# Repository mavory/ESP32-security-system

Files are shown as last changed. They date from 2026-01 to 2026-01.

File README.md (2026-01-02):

# ESP32 security system

It is a secure system that can use an RFID reader to let people into a building,...

## Why did I do this?

I don't even know... I previously did this project with an Arduino and so I decided to do it with my new ESP32!

## Features

- Web interface
- Can add new cards to the system (UID)
- It has a buzzer and an RGB LED for notification
- The motor acts like an automatic door

## Scripts

The entire script is only one and has about 300 lines, so just upload it via Arduino IDE and everything should work.

## How it works?

The RFID reader waits for the UID, if it is enabled in the system, the **motor** will turn, if not, it will not let you in. Turning the **buzzer** on or off can be controlled via a website running on the **IP address**.
- _Host mode:_ It can temporarily grant permission to a card for 2 minutes, and it can be extended or canceled
- _Lockdown mode:_ You can turn this mode on manually or set a time when it will turn on and turn off later. When it is on, the card cannot be scanned at that time and I cannot add a new card.
- _Scan new tag:_ You can add a tag permanently and change its name or remove it
- _Release latch:_ You can open the door manually
- You can also turn on/off the LED, buzzer, reader,...

### Home page:

### Admin page:


## 3D models

Here is a view of the top and bottom of the case:

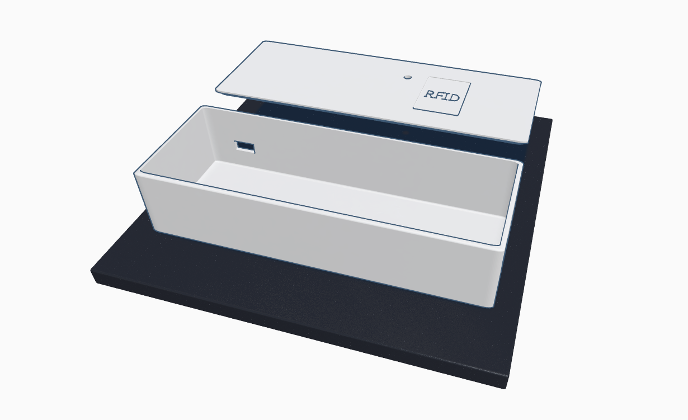
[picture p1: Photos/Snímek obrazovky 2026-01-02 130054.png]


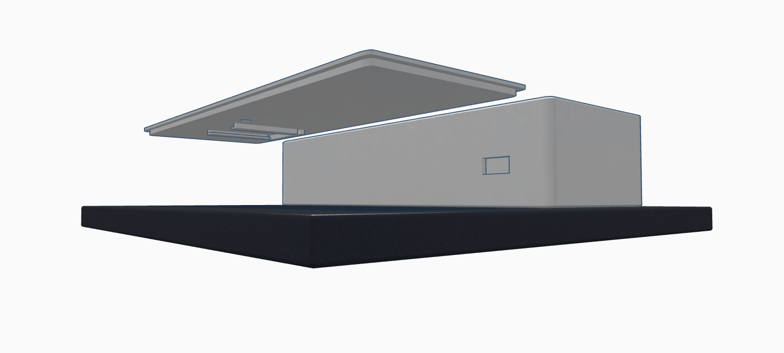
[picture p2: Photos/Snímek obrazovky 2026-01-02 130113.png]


## There is the final video of how it works!

_Here is a youtube video where you can see how it works:_ [Link](https://youtu.be/qIwMznMcJI0)



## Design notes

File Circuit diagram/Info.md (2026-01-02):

Documentation for the ESP32 RFID locking system!!

## Wiring

### RFID Reader (MFRC522)
- SDA (SS): GPIO 21
- SCK: GPIO 18
- MOSI: GPIO 23
- MISO: GPIO 19
- RST: GPIO 22
- 3.3V: 3.3V
- GND: GND

### Stepper Motor (ULN2003 Driver)
- IN1: GPIO 32
- IN2: GPIO 33
- IN3: GPIO 27
- IN4: GPIO 14
- VCC: 5V (External)
- GND: GND

### RGB LED Indicator
- Red: GPIO 25
- Green: GPIO 26
- Blue: GPIO 4
- GND: GND

### Buzzer
- Pin: GPIO 2
- GND: GND

---

## Technical Notes
- **Power:** The RFID module must be powered by 3.3V. Using 5V will damage the chip!

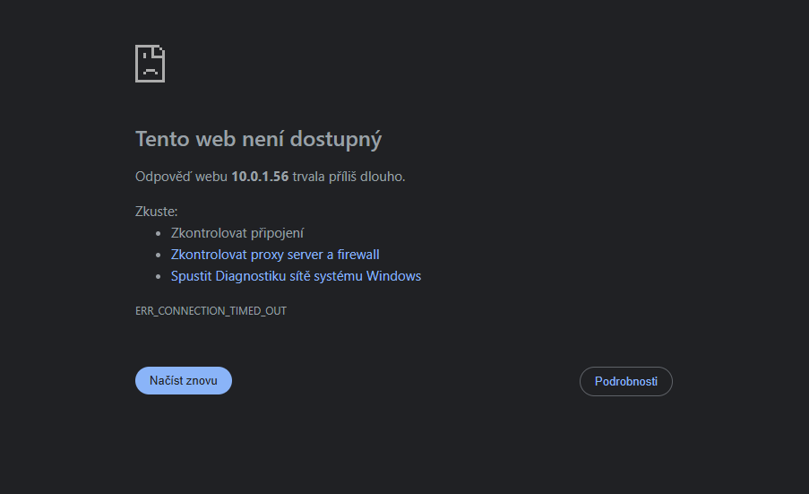
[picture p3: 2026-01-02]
Photos/Snímek obrazovky 2026-01-01 231753.png

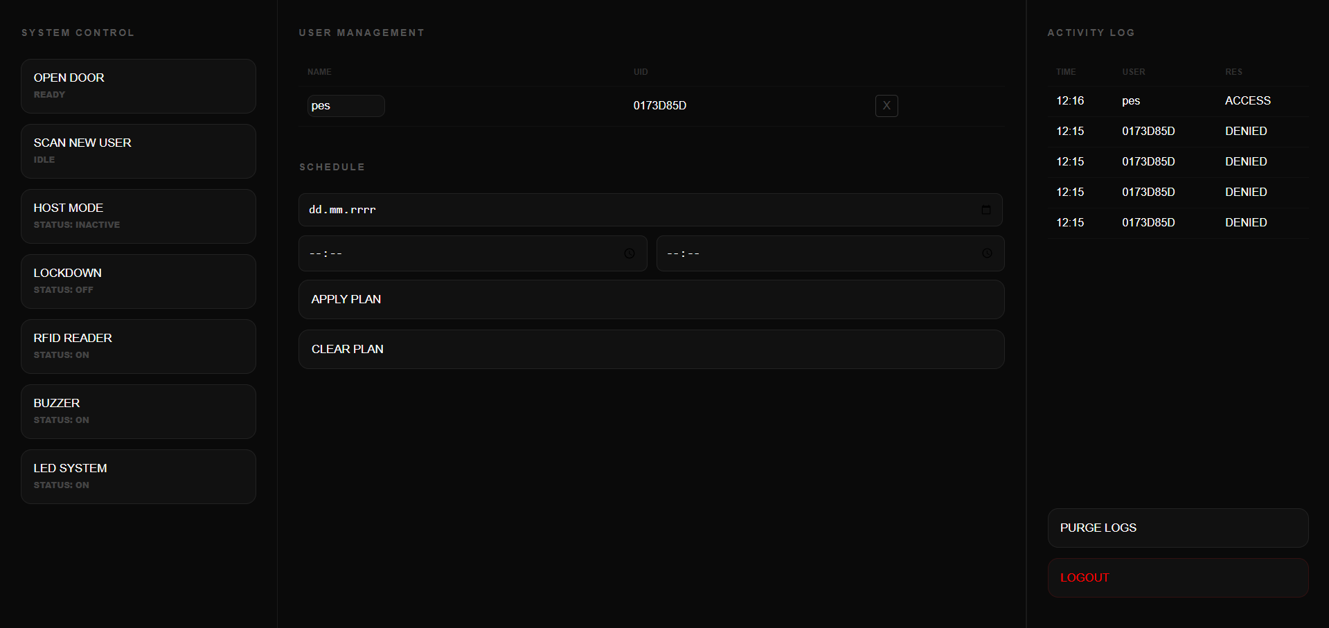
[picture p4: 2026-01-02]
Photos/Snímek obrazovky 2026-01-02 121619.png

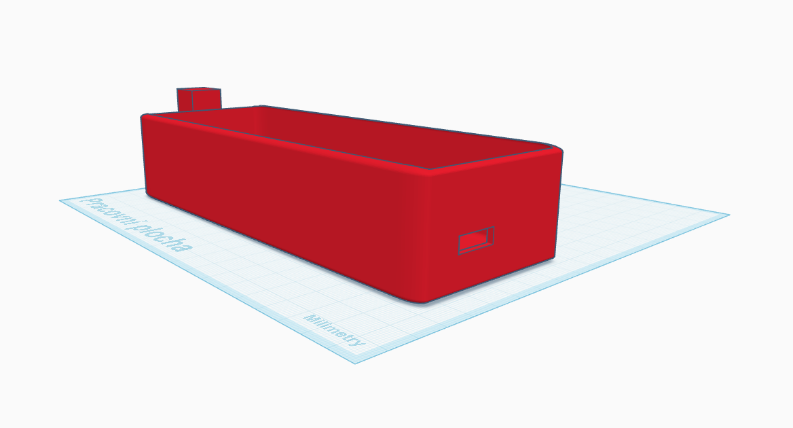
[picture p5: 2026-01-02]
Photos/Snímek obrazovky 2026-01-02 115620.png

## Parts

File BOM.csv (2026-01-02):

Item | Quantity | Link
ESP32 | 1 | https://www.aliexpress.com/item/1005009694232832.html?curPageLogUid=bPYYmnweQOZ8
RGB led | 1 | https://www.aliexpress.com/item/32977462875.html?scm_id=1007.40050.354490.0&scm-url=1007.40050.354490.0
Stepper motor | 1 | https://www.aliexpress.com/item/1005009055737108.html?curPageLogUid=D6r5ZVVTdLbr
Breadboard | 1 | https://www.aliexpress.com/item/1005009799908389.html
RFID module | 1 | https://www.aliexpress.com/item/1005001565846229.html
Buzzer | 1 | https://www.aliexpress.com/item/1005006260328559.html?curPageLogUid=u9zf8d5xh8uM
Cables | Idk...Much | https://www.aliexpress.com/item/1005002611994443.html?curPageLogUid=fx2zB0EGcu5H

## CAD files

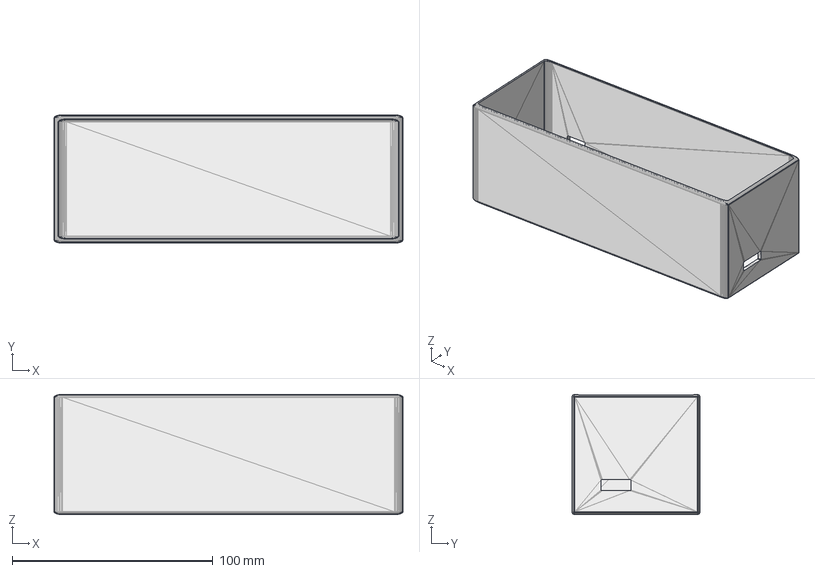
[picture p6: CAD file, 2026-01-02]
CAD/V2_Case.step
174.0 x 64.0 x 60.0 mm

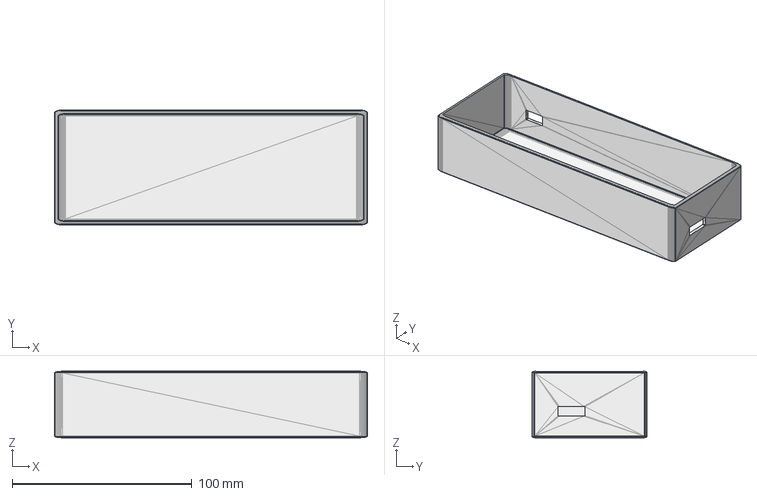
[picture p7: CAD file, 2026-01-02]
CAD/Case.step
174.0 x 64.0 x 37.0 mm

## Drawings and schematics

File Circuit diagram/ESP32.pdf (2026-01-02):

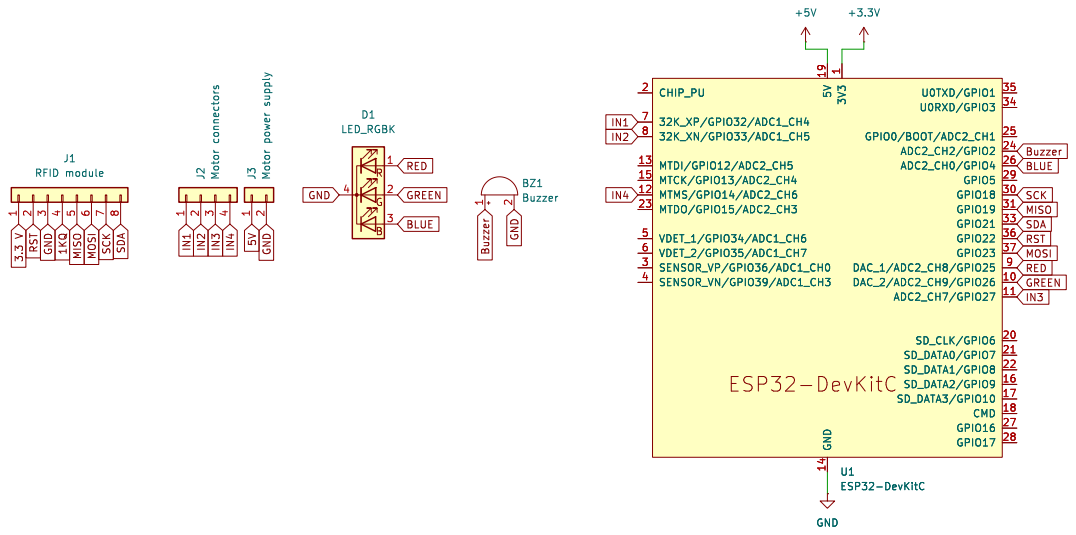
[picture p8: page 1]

Buzzer
BLUE
RST SCK GREEN MISO

2 BZ1 Buzzer SCK SDA IN1 IN45V IN3 GND IN2 MOSI

File: ESP32.kicad_sch Sheet: /
Id: 1/1 Title: ESP32 security system

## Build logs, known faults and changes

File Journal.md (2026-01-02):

# My Journal

This is a diary where I describe everything about how I created this project.

## So how much time did I spend on that?

I think I spent about 26.5 hours on this project.

## My worst hangups

- Unfortunately, I designed the bottom part of the case incorrectly, so I had to redo it completely.
- My RFID module hasn't been working for a while, so I had to solve this error as well.
- The website also didn't work for me because I broke it completely while coding.

## Timeline

### The beginning of my project!
I wanted to create an Arduino RFID system first, but later I decided to remake it and make it on my new ESP32!
I had to start from scratch, so I thought about how everything would work. I thought I could put a motor as a door and everything would be controlled via the web. When I had everything ready, I started taking things apart.
So it took me about 1.5 hours, because I had to dismantle the old project and think about the new one.



### Oh no! Breadboard problem
When my brain was ready, I started taking things apart and adjusting things on the breadboard!
I thought it would be fun, but it wasn't at all...
The ESP32 didn't fit on my breadboard and unfortunately I don't have another one, so I spent some time thinking about how to solve this problem.
Unfortunately, I struggled with this problem for quite a long time, because I was looking for other solutions, such as trying to solder it, but I backed away from that.
I came up with a solution, which is to put the ESP32 aside and thus have to use 2x more jumpers.



### Connecting things is my passion..
So when I solved this problem, I started wiring all the components, I have to say it was terrible.
I had to redo the whole layout a few times just to make sure everything fit on the breadboard.
I managed it and then I moved on to the next part!



### First steps to working code
Then I started coding. At first I tested if everything worked and I had to read some articles about how ESP32 works, because that was my first project with this microcontroller.
It took me about half an hour, but then I found out that it is very similar to Arduino!
So then everything went like clockwork (that's what I thought...) - Unfortunately, I had a lot of problems with the micro SD card reader, then with RFID,... but I managed it



### Big mistake for me
I thought everything would be fine, but after redoing the wiring, everything fell apart, the SD card reader and RFID reader didn't work, the RGB diode didn't light up properly, so I had to disconnect everything again and slowly start over.
I connected some pins and suddenly everything started working - for now...
( I didn't know I would have to do it again 💀 )



### A new beginning - for now
Well... I started coding again. Everything went pretty well, except for one thing. The SD card reader suddenly stopped working, so I tried to make a code for it to see if it would work now, and unfortunately, it didn't.
But I researched this bug for a long time because I couldn't figure it out.
This way, I was forced to remove the micro SD reader and live without it. I rewrote the entire code to make it work without the reader.



### Coding a script for ESP32
After this bug, I finally started coding and I have to say that it was terrible, my server crashed several times, it wouldn't load (as you can see in the photo) and I didn't know what to do.
Well, I tried different methods, but after a while I still ended up with the IP address.



### 1. Web interface
Coding was probably the hardest part for me, even though I made a lot of mistakes elsewhere. Coming up with a nice, but functional web interface was beyond my skills.
I tried to make just an admin panel without security, but that seemed strange to me, so I also tried to make a page for the public where they can see statistics and then I tried to make an admin page, which I didn't succeed at all. Either it wouldn't load at all or I couldn't connect the website to the ESP32.



### My dream look
I wasn't at all satisfied with how the temporary web interface looked, so I started reworking the code to get my dream look.
It took me a lot of effort, I tried a lot of options, but again I encountered an error that I had been solving for a long time, but after about half an hour it was solved and I could continue!
After some time, I decided that a modern and minimalist look with just a black and white theme would be best.



### Case design for everything
I took a break from programming for now and started thinking about how I would put everything in the case to make it look good!
My favorite and easy program to learn is Tinkercad. I normally use Fusion, but this is faster for me. When I started making some designs, I didn't notice that I was supposed to add a little space, so I fixed that. I had the sketch ready and suddenly I remembered that I was out of filament, so I ordered some new ones and hopefully they will arrive in the morning!



### A moment for quick coding
I had nothing else to do, so I started redesigning the web interface. It took me a while, but I still wasn't satisfied... At least it was a black and white look and minimalist.
Some buttons just didn't work properly, so I had to redesign it again later, but at least I knew where it was going.



### How to hide an RFID module?
I got my filament today, so I can start modeling the case! But first I have to measure everything so that everything fits in the case.
I had to measure mainly the RFID module so that they could make a smaller space for it to fit in there.
I thought for a while about how I would do it and came up with a solution: I would make a holder for the top part to hold it so it wouldn't be visible, but it should work.



### Making all parts of the case
It took me a while, but I've finished both parts of the case. There's a hole on the top for the RGB diode that signals the status, and there's also a marked hole for the RFID!

- Here is the top view:



- Here is the bottom view:



### 2. Web interface
Once I had the models ready, I went back to coding the website. There were some errors there, so I had to fix them. Sometimes the button wouldn't work for me or sometimes "Host mode" wouldn't work for me, so I fixed all that.
Unfortunately, I still have to redo the code, probably one more time, because I want to add some very interesting things!



### Circuit diagram!
I remembered that I still need to finish the Circuit diagram to show how it's connected. So I opened my favorite program - KICAD!
I started creating, but for example, for ESP32 I didn't know which model to use, I did some research and had to download some libraries to make it as similar as possible, but I managed it quite quickly, in my experience, in about an hour and a half.
The hardest part for me was probably finding what symbols to use, for example, I didn't know what symbol to use for the motor, but I guess I got the hang of it.

- Circuit diagram:



### Printing 3D models
I'm already printing the first part! Hopefully it will work and everything will fit.
Unfortunately, I've found a problem that when I want to scan the UID, the reader doesn't work at all, so I have to try to find the problem and solve it as quickly as possible!



### Final code for the website
I have to say it with joy, but I already have a finished web interface, which looks very good to me! There are buttons to turn off the buzzer, RGB diodes, readers,...
It all took me a lot of time and I have to say that it was worth it. The code is about 330 lines, so it's not that long. I also modified the homepage to match the new design.

- Home page:



- Admin page:



### Exporting files
I'm very close to the end, just need to finish a few wiring things and I think it'll be ready! I already have the last part printed, but the supports were harder to remove, so I had to spend 30 minutes cutting the plastic to make it fit properly!
I've also started exporting the files, which I'll later upload to GitHub, where everything is! I still have to finish the information and connections, so I still have a long way to go.



### Remaking a 3D model
How to say it.... I started putting all the things in the box, everything fit except for one SMALL THING... CABLES
I made the box too short, so I can't close the cables and so on with it anymore. So I had to redo the case again and hopefully it will be good.



### GitHub editing
So I started 3D printing the case, but I decided to print it in white and the top in black! In the meantime, I continued to write and upload things to GitHub to make sure everything met the requirements.
I'm very excited that I got through all the hurdles, because at first I thought I just couldn't do it.
For now, I've made a BOM, I've also uploaded the completed code, I've uploaded the Circuit diagram and some information to make it easier to connect.



### Putting things in the case
I finished the last part - the case. It took me a while to remove the supports, cut off the gaps and I really like this design! The cable to the motor runs from the side and the power cable that powers the ESP32 runs from the back!
I glued the top with normal super glue and put the buzzer close to the hole so that it would be better heard, but I decided that I would still edit the code in the end to fine-tune the RFID, but mainly to increase the "volume" of the buzzer, because it was not audible before.



**After about +- 26.5 hours I have finished this project and I am very proud of it. I was able to create my first project with ESP32!**
## How it works:
The RFID reader waits for the UID, if it is enabled in the system, the **motor** will turn, if not, it will not let you in. Turning the **buzzer** on or off can be controlled via a website running on the **IP address**.
After **10 attempts**, the reader is blocked for a while to prevent unknown cards from being tried over and over again.
- _Host mode:_ It can temporarily grant permission to a card for 2 minutes, and it can be extended or canceled
- _Lockdown mode:_ You can turn this mode on manually or set a time when it will turn on and turn off later. When it is on, the card cannot be scanned at that time and I cannot add a new card.
- _Scan new tag:_ You can add a tag permanently and change its name or remove it
- _Release latch:_ You can open the door manually
- You can also turn on/off the LED, buzzer, reader,...

_Here is a youtube video where you can see how it works:_ [Link](https://youtu.be/qIwMznMcJI0)

## Wiring:

### RFID Reader (MFRC522)
- SDA (SS): GPIO 21
- SCK: GPIO 18
- MOSI: GPIO 23
- MISO: GPIO 19
- RST: GPIO 22
- 3.3V: 3.3V
- GND: GND

### Stepper Motor (ULN2003 Driver)
- IN1: GPIO 32
- IN2: GPIO 33
- IN3: GPIO 27
- IN4: GPIO 14
- VCC: 5V (External)
- GND: GND

### RGB LED Indicator
- Red: GPIO 25
- Green: GPIO 26
- Blue: GPIO 4
- GND: GND

### Buzzer
- Pin: GPIO 2
- GND: GND

### Technical Notes
- **Power:** The RFID module must be powered by 3.3V. Using 5V will damage the chip!

## Scripts
The entire script is only one and has about **300 lines**, so just upload it via **Arduino IDE** and everything should work.

## Libraries:

```
- MFRC522.h
- ESPAsyncWebServer.h
- AsyncTCP.h
- Stepper.h
```

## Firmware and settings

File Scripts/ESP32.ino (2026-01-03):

#include <Arduino.h>
#include <SPI.h>
#include <MFRC522.h>
#include <LittleFS.h>
#include <WiFi.h>
#include <ESPAsyncWebServer.h>
#include <Stepper.h>
#include <deque>
#include "time.h"

// PINOUT!!
const char* ssid = "WIFI";
const char* password = "PASS";
const char* adminUser = "admin";
const char* adminPass = "admin123";

#define SCK_PIN 18
#define MISO_PIN 19
#define MOSI_PIN 23
#define SS_PIN 21
#define RST_PIN 22
#define STEP1 32
#define STEP2 33
#define STEP3 27
#define STEP4 14
#define L_R 25
#define L_G 26
#define L_B 4
#define BUZZ 2

//udání
MFRC522 rfid(SS_PIN, RST_PIN);
AsyncWebServer server(80);
Stepper door(2048, STEP1, STEP3, STEP2, STEP4);

bool lockdownManual = false;
bool readerOn = true;
bool ledsOn = true;
bool buzzOn = true;
bool scanMode = false;
int okC = 0, failC = 0, strikes = 0;
unsigned long blockStart = 0;

bool hostModeWaiting = false;
String hostCardUID = "";
unsigned long hostEndTime = 0; // Změněno z hostStartTime jen kvůli odpočtu

String schedDate = "";
int sH = -1, sM = -1, eH = -1, eM = -1;

unsigned long motorStartTime = 0;
int motorPhase = 0; 
bool greenFeedback = false;
unsigned long redFeedbackEnd = 0;

struct User { String id; String name; String last; };
std::vector<User> users;
struct Log { String t; String n; String res; };
std::deque<Log> logs;

void setLED(int r, int g, int b) { 
  // Pokud jsou LED vypnuté v nastavení, ale probíhá feedback nebo motor, stejně se rozsvítí
  bool override = (motorPhase > 0 || greenFeedback || redFeedbackEnd > millis() || strikes >= 10);
  if (!ledsOn && !override) {
    digitalWrite(L_R, LOW); digitalWrite(L_G, LOW); digitalWrite(L_B, LOW);
    return;
  }
  digitalWrite(L_R, r > 0 ? HIGH : LOW);
  digitalWrite(L_G, g > 0 ? HIGH : LOW);
  digitalWrite(L_B, b > 0 ? HIGH : LOW);
}

// Vyšší frekvence pro pocitově vyšší hlasitost
void sound(int f, int d) { if(buzzOn) tone(BUZZ, f, d); }
void actionBeep() { sound(2500, 50); } // Pronikavější pípnutí

void loadUsers() {
  users.clear();
  if(!LittleFS.exists("/u.dat")) return;
  File f = LittleFS.open("/u.dat", "r");
  while(f.available()){
    String i = f.readStringUntil(':'); String n = f.readStringUntil('|'); String l = f.readStringUntil('\n');
    i.trim(); n.trim(); l.trim();
    if(i.length()>0) users.push_back({i, n, l});
  }
  f.close();
}

void saveUsers() {
  File f = LittleFS.open("/u.dat", "w");
  if(!f) return;
  for(auto const& u : users) f.printf("%s:%s|%s\n", u.id.c_str(), u.name.c_str(), u.last.c_str());
  f.close();
}

void addLog(String name, String res) {
  struct tm ti; getLocalTime(&ti); char ts[10]; strftime(ts, 10, "%H:%M", &ti);
  if(logs.size() >= 15) logs.pop_back();
  logs.push_front({String(ts), name, res});
}

bool isLockdownActive() {
  struct tm ti; if(!getLocalTime(&ti)) return lockdownManual;
  char buf[11]; strftime(buf,11,"%Y-%m-%d",&ti);
  if (schedDate != "" && String(buf) == schedDate) {
    int nowMin = ti.tm_hour * 60 + ti.tm_min;
    int startMin = sH * 60 + sM;
    int endMin = eH * 60 + eM;
    if (nowMin >= startMin && nowMin < endMin) return true;
  }
  return lockdownManual;
}

//začátek toho nechutnýho kódu (Ale je uspornej)
const char index_html[] PROGMEM = R"rawliteral(
<!DOCTYPE html><html><head><meta charset="UTF-8"><style>
body{background:#000;color:#fff;font-family:sans-serif;display:flex;justify-content:center;align-items:center;height:100vh;margin:0;}
.card{width:420px;text-align:center;padding:40px;border:1px solid #111;border-radius:24px;background:#050505;}
h1{font-size:0.7rem;letter-spacing:4px;color:#444;text-transform:uppercase;margin-bottom:40px;}
#st{font-size:2.8rem;font-weight:200;margin-bottom:10px;}
#scInfo{font-size:0.8rem;color:#ff9500;margin-bottom:30px;height:20px;}
table{width:100%;font-size:0.75rem;color:#666;border-collapse:collapse;} td{padding:12px;border-bottom:1px solid #111;text-align:left;}
.admin-link{display:block;margin-top:40px;color:#222;text-decoration:none;font-size:0.65rem;}
</style></head><body><div class="card"><h1>SECURITY SYSTEM</h1><div id="st">...</div><div id="scInfo"></div><table id="lb"></table><a href="/admin" class="admin-link">SYSTEM ADMINISTRATION</a></div>
<script>async function up(){const r=await fetch('/api/st');const d=await r.json();
document.getElementById('st').innerText=d.isL?'LOCKDOWN':(d.isB?'BLOCKED':'ONLINE');
document.getElementById('st').style.color=d.isL?'#ff3b30':'#ffffff'; 
document.getElementById('scInfo').innerText=d.scD?`Planned Lockdown: ${d.scD} ${d.scS}-${d.scE}`:'';
let h='';d.logs.slice(0,5).forEach(l=>h+=`<tr><td>${l.t}</td><td>${l.n}</td><td>${l.r}</td></tr>`);document.getElementById('lb').innerHTML=h;}setInterval(up,2000);up();</script></body></html>
)rawliteral";

const char admin_html[] PROGMEM = R"rawliteral(
<!DOCTYPE html><html><head><meta charset="UTF-8"><style>
body{background:#000;color:#fff;font-family:sans-serif;margin:0;overflow:hidden;height:100vh;}
.main{display:grid;grid-template-columns:320px 1fr 350px;height:100vh;background:#1a1a1a;gap:1px;}
.col{background:#0a0a0a;padding:28px;overflow-y:auto;display:flex;flex-direction:column;}
h2{font-size:0.7rem;color:#555;text-transform:uppercase;letter-spacing:2px;margin-bottom:24px;}
.btn{background:#111;border:1px solid #222;color:#fff;padding:16px;cursor:pointer;margin-bottom:12px;width:100%;text-align:left;border-radius:12px;}
.btn:disabled{opacity:0.1;cursor:not-allowed;}
.btn-status{display:block;font-size:0.6rem;color:#444;margin-top:4px;font-weight:800;text-transform:uppercase;}
.h-box{background:#001a33;padding:15px;border-radius:12px;margin-bottom:15px;border:1px solid #003366;}
input{background:#111;border:1px solid #222;color:#fff;padding:12px;width:calc(100% - 28px);margin-bottom:12px;border-radius:10px;outline:none;}
table{width:100%;font-size:0.8rem;border-collapse:collapse;} td,th{padding:12px 10px;border-bottom:1px solid #111;}
th{text-align:left;color:#333;font-size:0.6rem;}
</style></head><body>
<div class="main">
  <div class="col">
    <h2>SYSTEM CONTROL</h2>
    <button class="btn" onclick="f('/api/open')">RELEASE LATCH<span class="btn-status">READY</span></button>
    <button class="btn" id="btnS" onclick="f('/api/scan')">SCAN NEW TAG<span id="statScan" class="btn-status">IDLE</span></button>
    <div id="hArea"></div>
    <button class="btn" id="btnH" onclick="f('/api/host')">HOST ACCESS<span id="statHost" class="btn-status">INACTIVE</span></button>
    <button class="btn" onclick="f('/api/t-l')">LOCKDOWN MODE<span id="statLock" class="btn-status">OFF</span></button>
    <button class="btn" onclick="f('/api/t-r')">RFID READER<span id="statRead" class="btn-status">ON</span></button>
    <button class="btn" onclick="f('/api/t-b')">BUZZER FEEDBACK<span id="statBuzz" class="btn-status">ON</span></button>
    <button class="btn" onclick="f('/api/t-led')">STATUS LIGHTS<span id="statLed" class="btn-status">ON</span></button>
  </div>
  <div class="col">
    <h2>USER DIRECTORY</h2><div id="uList"></div>
    <h2 style="margin-top:40px">SCHEDULER</h2>
    <div id="scActive" style="font-size:0.7rem;color:#555;margin-bottom:10px"></div>
    <input type="date" id="sd"><div style="display:flex;gap:10px"><input type="time" id="ss"><input type="time" id="se"></div>
    <button class="btn" onclick="setS()">APPLY SCHEDULE</button><button class="btn" onclick="f('/api/s-clr')">CLEAR SCHEDULE</button>
  </div>
  <div class="col">
    <h2>ACTIVITY LOG</h2><table id="lb"></table>
    <button class="btn" style="margin-top:auto" onclick="f('/api/clear')">PURGE ALL LOGS</button>
    <button class="btn" style="color:#ff453a;border-color:#331111;" onclick="location.href='/logout'">EXIT SESSION</button>
  </div>
</div>
<script>
function f(u){fetch(u);setTimeout(load,200);}
function setS(){fetch(`/api/sched?d=${document.getElementById('sd').value}&s=${document.getElementById('ss').value}&e=${document.getElementById('se').value}`);setTimeout(load,200);}
async function load(){
  const r=await fetch('/api/st');const d=await r.json();
  document.getElementById('btnS').disabled = d.isL;
  document.getElementById('btnH').disabled = d.isL;
  document.getElementById('statLock').innerText='STATUS: '+(d.isL?'ACTIVE':'OFF');
  document.getElementById('statRead').innerText='STATUS: '+(d.rO?'ON':'OFF');
  document.getElementById('statBuzz').innerText='STATUS: '+(d.bO?'ON':'OFF');
  document.getElementById('statLed').innerText='STATUS: '+(d.lO?'ON':'OFF');
  document.getElementById('statHost').innerText='STATUS: '+(d.hW?'WAITING':'INACTIVE');
  document.getElementById('scActive').innerText = d.scD ? `Scheduled: ${d.scD} (${d.scS}-${d.scE})` : 'No schedule set';
  if(d.hRem > 0) {
    document.getElementById('hArea').innerHTML = `<div class="h-box"><div style="font-size:0.7rem;color:#00aaff">HOST 1 ACTIVE</div><div style="font-size:1.1rem;margin:5px 0">${d.hRem}s remaining</div><button onclick="f('/api/h-plus')" style="background:#003366;border:none;color:white;padding:5px 8px;border-radius:4px;cursor:pointer">+2m</button><button onclick="f('/api/h-del')" style="background:#330000;border:none;color:white;padding:5px 8px;border-radius:4px;cursor:pointer;margin-left:5px">Revoke</button></div>`;
  } else document.getElementById('hArea').innerHTML = '';
  let lh='<tr><th>TIME</th><th>ENTITY</th><th>RESULT</th></tr>';
  d.logs.forEach(l=>lh+=`<tr><td>${l.t}</td><td>${l.n}</td><td>${l.r}</td></tr>`);
  document.getElementById('lb').innerHTML=lh;
  const ur=await fetch('/api/ulist');const ud=await ur.json();
  let uh='<table><tr><th>NAME</th><th>UID</th><th></th></tr>';
  ud.forEach(u=>uh+=`<tr><td><input style="margin:0;padding:4px;width:100px" value="${u.n}" onchange="ren('${u.i}',this.value)"></td><td><span style="color:#444">${u.i}</span></td><td><button style="background:none;border:none;color:#ff453a;cursor:pointer" onclick="del('${u.i}')">DEL</button></td></tr>`);
  document.getElementById('uList').innerHTML=uh+'</table>';
}
function ren(i,n){fetch(`/api/rename?id=${i}&n=${n}`);}
function del(i){if(confirm('Delete?')){fetch(`/api/del?id=${i}`);setTimeout(load,200);}}
load(); setInterval(load, 2000);
</script></body></html>
)rawliteral";

void setup() {
  Serial.begin(115200);
  if(!LittleFS.begin(true)){ LittleFS.format(); LittleFS.begin(); }
  loadUsers();
  pinMode(L_R, OUTPUT); pinMode(L_G, OUTPUT); pinMode(L_B, OUTPUT); 
  pinMode(BUZZ, OUTPUT); pinMode(RST_PIN, OUTPUT);

  SPI.begin(SCK_PIN, MISO_PIN, MOSI_PIN, SS_PIN);
  Serial.println("INITIALIZING RFID...");
  while(true) {
    digitalWrite(RST_PIN, LOW); delay(50); digitalWrite(RST_PIN, HIGH); delay(50);
    rfid.PCD_Init();
    rfid.PCD_SetAntennaGain(rfid.RxGain_max);
    byte v = rfid.PCD_ReadRegister(rfid.VersionReg);
    Serial.print("RFID Check: 0x"); Serial.println(v, HEX);
    if(v != 0x00 && v != 0xFF) {
      Serial.println(">> RFID SUCCESSS! Module connected. <<");
      sound(3000, 100); delay(150); sound(4000, 100); 
      break; 
    }
    delay(1000);
  }

  WiFi.begin(ssid, password);
  configTime(3600, 3600, "pool.ntp.org"); 

  server.on("/", HTTP_GET, [](AsyncWebServerRequest *r){ r->send_P(200, "text/html", index_html); });
  server.on("/admin", HTTP_GET, [](AsyncWebServerRequest *r){
    if(!r->authenticate(adminUser, adminPass)) return r->requestAuthentication();
    r->send_P(200, "text/html", admin_html);
  });
  server.on("/logout", HTTP_GET, [](AsyncWebServerRequest *r){
    r->send(401, "text/html", "<html><script>window.location.href='/';</script></html>");
  });

  server.on("/api/st", HTTP_GET, [](AsyncWebServerRequest *r){
    long hRem = (hostEndTime > millis()) ? (hostEndTime - millis()) / 1000 : 0;
    String j = "{ \"isL\":" + String(isLockdownActive()?"true":"false") + ",\"isB\":" + String(strikes>=10?"true":"false");
    j += ",\"rO\":" + String(readerOn?"true":"false") + ",\"bO\":" + String(buzzOn?"true":"false") + ",\"lO\":" + String(ledsOn?"true":"false") + ",\"hW\":" + String(hostModeWaiting?"true":"false");
    j += ",\"scD\":\"" + schedDate + "\",\"scS\":\"" + (sH<10?"0":"")+String(sH)+":"+(sM<10?"0":"")+String(sM) + "\",\"scE\":\"" + (eH<10?"0":"")+String(eH)+":"+(eM<10?"0":"")+String(eM) + "\"";
    j += ",\"hRem\":" + String(hRem);
    j += ",\"logs\":[";
    for(int i=0; i<logs.size(); i++) j += "{\"t\":\""+logs[i].t+"\",\"n\":\""+logs[i].n+"\",\"r\":\""+logs[i].res+"\"}" + (i<logs.size()-1?",":"");
    j += "]}"; r->send(200, "application/json", j);
  });

  server.on("/api/ulist", HTTP_GET, [](AsyncWebServerRequest *r){
    String j = "[";
    for(int i=0; i<users.size(); i++) j += "{\"i\":\""+users[i].id+"\",\"n\":\""+users[i].name+"\"}" + (i<users.size()-1?",":"");
    j += "]"; r->send(200, "application/json", j);
  });

  server.on("/api/scan", [](AsyncWebServerRequest *r){ if(!isLockdownActive()) scanMode = true; actionBeep(); r->send(200); });
  server.on("/api/host", [](AsyncWebServerRequest *r){ if(!isLockdownActive()) hostModeWaiting = true; actionBeep(); r->send(200); });
  server.on("/api/h-plus", [](AsyncWebServerRequest *r){ if(hostEndTime > millis()) hostEndTime += 120000; actionBeep(); r->send(200); });
  server.on("/api/h-del", [](AsyncWebServerRequest *r){ hostEndTime = 0; hostCardUID = ""; actionBeep(); r->send(200); });
  server.on("/api/t-l", [](AsyncWebServerRequest *r){ lockdownManual = !lockdownManual; actionBeep(); r->send(200); });
  server.on("/api/t-r", [](AsyncWebServerRequest *r){ readerOn = !readerOn; actionBeep(); r->send(200); });
  server.on("/api/t-b", [](AsyncWebServerRequest *r){ buzzOn = !buzzOn; actionBeep(); r->send(200); });
  server.on("/api/t-led", [](AsyncWebServerRequest *r){ ledsOn = !ledsOn; actionBeep(); r->send(200); });
  server.on("/api/s-clr", [](AsyncWebServerRequest *r){ schedDate = ""; actionBeep(); r->send(200); });
  server.on("/api/clear", [](AsyncWebServerRequest *r){ logs.clear(); actionBeep(); r->send(200); });
  server.on("/api/rename", [](AsyncWebServerRequest *r){ String id = r->arg("id"), n = r->arg("n"); for(auto &u : users) if(u.id == id) u.name = n; saveUsers(); r->send(200); });
  server.on("/api/del", [](AsyncWebServerRequest *r){ String id = r->arg("id"); users.erase(std::remove_if(users.begin(), users.end(), [&](User u){return u.id == id;}), users.end()); saveUsers(); r->send(200); });
  server.on("/api/open", [](AsyncWebServerRequest *r){ if(motorPhase==0){ greenFeedback=true; motorPhase=1; actionBeep(); } r->send(200); });
  server.on("/api/sched", [](AsyncWebServerRequest *r){ schedDate = r->arg("d"); sH = r->arg("s").substring(0,2).toInt(); sM = r->arg("s").substring(3,5).toInt(); eH = r->arg("e").substring(0,2).toInt(); eM = r->arg("e").substring(3,5).toInt(); actionBeep(); r->send(200); });

  server.begin();
}

void loop() {
  unsigned long now = millis();
  if (now % 5000 == 0) rfid.PCD_SetAntennaGain(rfid.RxGain_max);
  if(strikes >= 10 && (now - blockStart > 120000)) strikes = 0;

  door.setSpeed(12);
  if (motorPhase == 1) { 
    setLED(0, 255, 0); // VYNUCENÍ ZELENÉ PŘED POHYBEM
    delay(100); 
    door.step(1024); 
    motorStartTime = now; 
    motorPhase = 2; 
  }
  else if (motorPhase == 2 && (now - motorStartTime > 3000)) { motorPhase = 3; }
  else if (motorPhase == 3) { 
    setLED(0, 255, 0); // DRŽET ZELENOU PŘI NÁVRATU
    door.step(-1024); 
    motorPhase = 0; 
    greenFeedback = false; 
  }

  // LOGIKA STAVOVÉ DIODY
  if (strikes >= 10) setLED(255, 0, 0);
  else if (motorPhase > 0 || greenFeedback) setLED(0, 255, 0);
  else if (now < redFeedbackEnd) setLED(255, 0, 0);
  else if (scanMode) setLED(255, 255, 0);
  else if (hostModeWaiting) setLED(0, 0, 255);
  else if (isLockdownActive()) setLED(255, 0, 0);
  else setLED(10, 10, 20); // Standby modrá

  if (readerOn && !isLockdownActive() && strikes < 10 && motorPhase == 0) {
    rfid.PCD_Init(); 
    if (rfid.PICC_IsNewCardPresent() && rfid.PICC_ReadCardSerial()) {
      String id = "";
      for(byte i=0; i<rfid.uid.size; i++) id += (rfid.uid.uidByte[i]<0x10?"0":"")+String(rfid.uid.uidByte[i], HEX);
      id.toUpperCase();

      if(scanMode) {
        bool exists = false; for(auto &u : users) if(u.id == id) exists = true;
        if(!exists) { users.push_back({id, "NEW USER", "NEVER"}); saveUsers(); }
        scanMode = false; sound(2000, 100);
      } 
      else if(hostModeWaiting) {
        hostCardUID = id; hostEndTime = now + 300000;
        hostModeWaiting = false; sound(2000, 200); addLog("HOST 1 SET", id);
      } 
      else {
        bool allowed = (id == hostCardUID && now < hostEndTime); 
        String name = (id == hostCardUID) ? "HOST 1" : "UNKNOWN";
        for(auto &u : users) if(u.id == id){ 
          allowed = true; name = u.name; 
          struct tm ti; getLocalTime(&ti); char ts[20]; strftime(ts, 20, "%d.%m %H:%M", &ti);
          u.last = String(ts); break; 
        }
        if(allowed) {
          addLog(name, "APPROVED"); strikes = 0; greenFeedback = true; 
          setLED(0, 255, 0); // OKAMŽITÝ FEEDBACK
          sound(1500, 100); sound(2000, 150); 
          motorPhase = 1; 
          saveUsers();
        } else {
          strikes++; addLog(id, "DENIED"); 
          redFeedbackEnd = now + 2000; 
          setLED(255, 0, 0); // OKAMŽITÝ FEEDBACK
          if(strikes >= 10) blockStart = now; 
          sound(400, 500); // HLASITÉ DLOUHÉ "ERROR" BZUČENÍ
        }
      }
      rfid.PICC_HaltA(); rfid.PCD_StopCrypto1();
      delay(1500); 
    }
  }
}

//miluju když je to hotove - @MAVORY

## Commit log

2026-01-02 Step files
    [Case.step]
2026-01-02 Circuit diagram
    [ESP32.kicad_sch]
2026-01-02 Journal.md
    Updated project time and added detailed project completion notes, including wiring and functionality of components.
